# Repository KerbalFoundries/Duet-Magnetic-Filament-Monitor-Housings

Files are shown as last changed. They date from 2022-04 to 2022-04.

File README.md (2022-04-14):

# Duet-Magnetic-Filament-Monitor-Housings
Redesigned MFM housing for reliable FDM printin

Critical/important print settings:

**0.1mm layer height**. Or anything that divides into that cleanly. NOT, say, 0.16mm because it's the *magic* layer height of your machine. 
**0.4mm wall line width**. Or width that cleanly divides into 1.2mm.

Notes and to expand on the above:

The only super critical print setting is to use 0.1mm layer height. I really cannot stress this enough. Moving down to 0.05mm is fine, as is any other layer height the divides neatly into 0.1. Anything else is likely to land you with some "odd" dimensions that are really quite important. Otherwise, just do what you'd normally do for accurate functional prints. In Cura, the "Horizontal Expansion" setting can be quite handy to compensate for any deviation of your printer - I'm sure other slicers have similar settings.

I've designed for 0.4mm line width, so best to stick to that. 10-20% infill of any type that ties the walls to the top/bottom will work fine. I used lines an gyroid while testing. You should get 3 x whole lines in the 1.2mm "walls" of the lid.

The lid might need a light deburr if you get some elephants foot on the first layer.

I opted for using flanged RC servo screws to mount the board, though you can easily drill and tap to
M2.5 for the board mounts. All the supplied hardware is used as standard otherwise.

Push the PTFE tube into the housings so it's close to, but not interfering with the hobbed section. This runs in further than the official housing and is best done before the rotating mag assembly is installed so you can be sure where it ends up. Running the point of a knife or deburring tool inside the entry to the outgoing PTFE completely eliminates any snag when loading filament.

The bottom bearing is best pressed in with the head of an M5 cap head screw if this is required. This puts the force purely on the outer race, though not much should be needed all other things being equal. As explained in the original post the seats have a slight taper which seems to account nicely for variations in prints and gives a snug fit without any fussing. The bearings snap nicely into place on all my prints now with no play or fettling needed.

The idler carrier halves will need gluing together around the bearing as per the original and need no special attention. I'd advise a tiny blob of glue where the stubs meet inside the bearing, but careful with the bearing itself, obviously.

Thanks to the Duet team for the support while I was developing this, it really is first class!

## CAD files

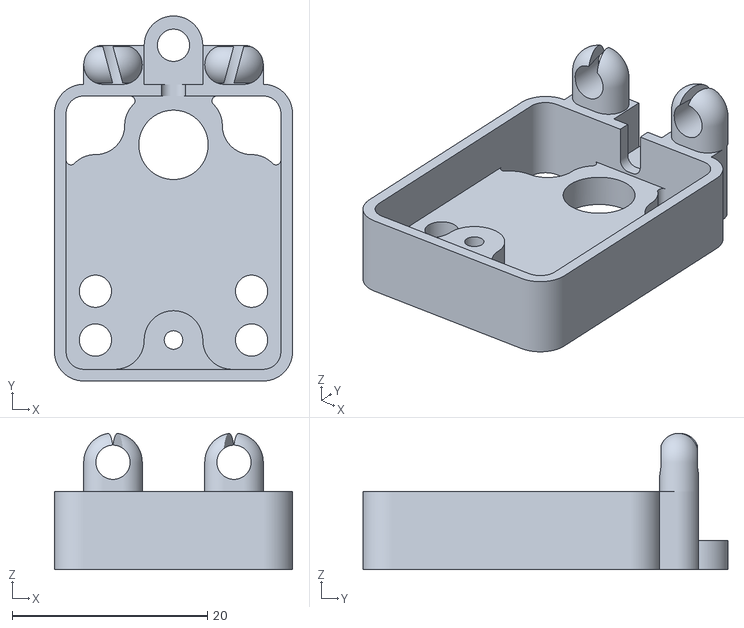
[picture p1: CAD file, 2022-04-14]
V2 Magnetic Assembly/MFM Housing - Lo-Fi Lid - mag V2.stl
24.4 x 37.4 x 14.0

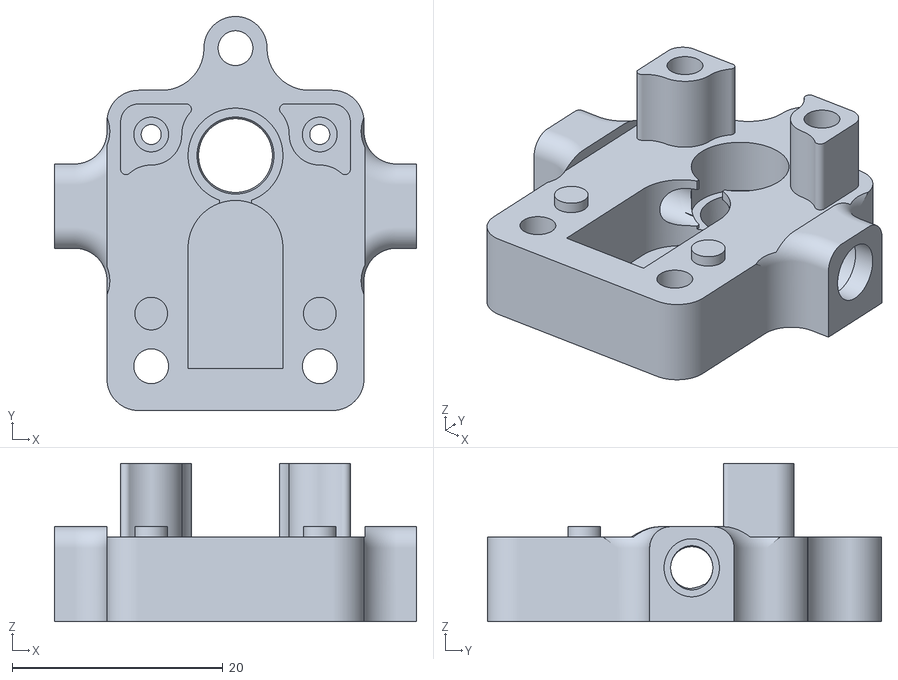
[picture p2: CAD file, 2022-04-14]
V2 Magnetic Assembly/MFM Housing - Lo-Fi Base - mag V2.stl
34.4 x 37.4 x 15.0

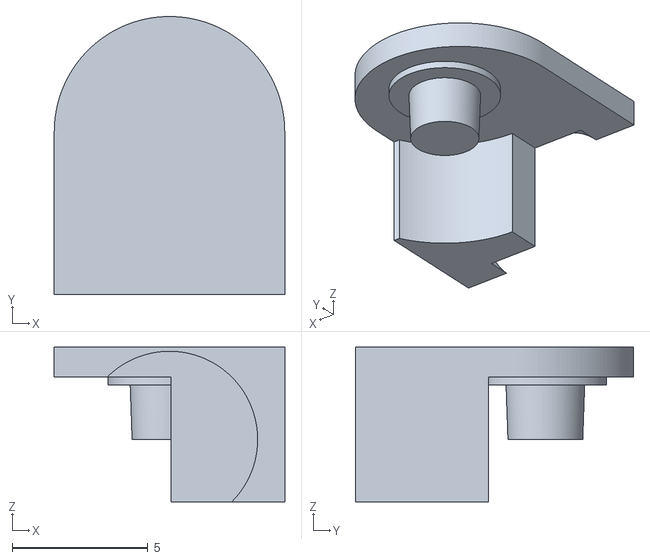
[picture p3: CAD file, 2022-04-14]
V2 Magnetic Assembly/MK2 MFM Idler - Idler Carrier V2.stl
8.50 x 10.3 x 5.70

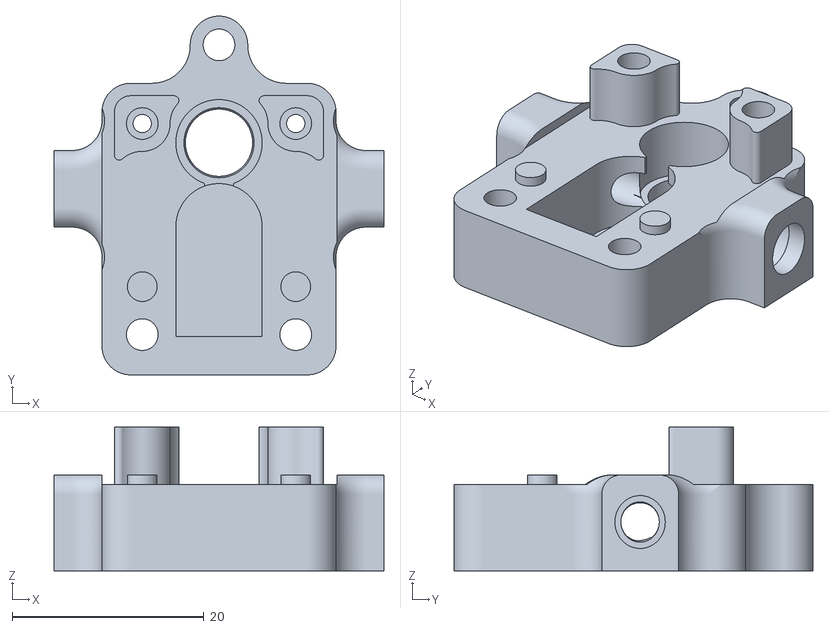
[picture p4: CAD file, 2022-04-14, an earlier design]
V1 Magnetic Assembly/MFM Housing - Lo-Fi Base - mag V1.stl
34.4 x 37.4 x 15.0

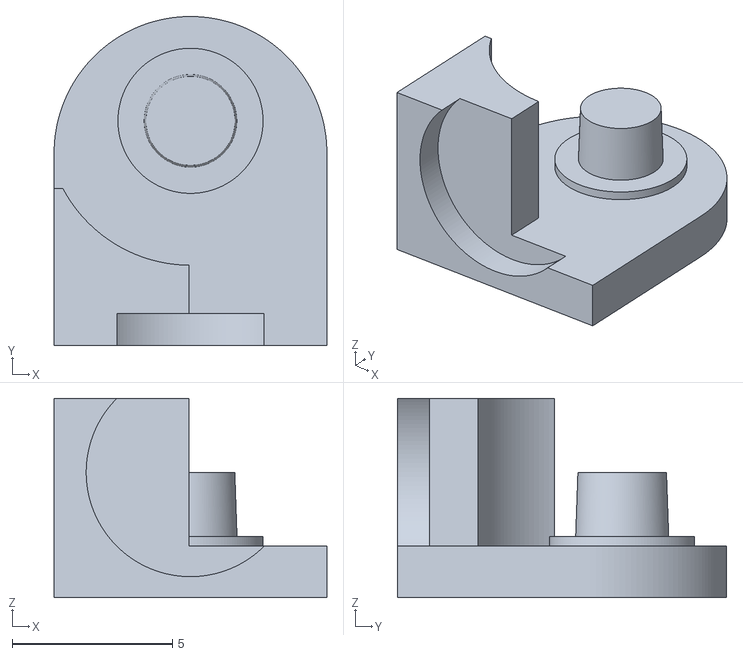
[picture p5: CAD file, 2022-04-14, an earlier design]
V1 Magnetic Assembly/MFM Idler - Idler Mount V1.stl
8.50 x 10.3 x 6.20

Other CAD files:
V1 Magnetic Assembly/MFM Housing - Lo-Fi Lid - mag V1.stl
